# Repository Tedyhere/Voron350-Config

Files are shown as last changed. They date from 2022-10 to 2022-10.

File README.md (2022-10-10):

# Voron350-Config
Config for Voron350 Kit offered by CTRL-Pew

This Kit comes with the PCB Toolboard for the Extruder so be sure to print the Motor Plate for PCB board.
Also print these Parts including the files in the Clockwork folder.
https://github.com/VoronDesign/Voron-Hardware/tree/master/Afterburner_Toolhead_PCB/STLs/Clockwork

For the z Endstop I used the PCB Board Version and drilled 1.5mm holes to match the PCB board for the z endstop in the bottom.

Be sure to check the Parts Cooling and Hotend Fan wire connectors, mine were wire up reverse to what the toolboard required, this is easy to fix, I used a sim card tray tool to push down on the tiny tabs on the connectors and pulled the wires out and swapped them.

You will need to rewire your motors to EXACTLY MATCH the colors on the wiring sheet. I had to extend the B motor on the left side with the Black wire included.  I went ahead and redid both motors to give more length.. I used 4 pin Black connectors included.. Be sure to do 1 wire and connector at a time to ensure you don't cross up wires.  Doing this will make it easier in case a Motor goes bad.

For the Bed you will need to tap the two holes for the Ground and the Thermal fuse.  Follow the directions for the wiring, it seems confusing but..

My heating pad looked like this..

Wires with the wires exiting down.

Left Red wire goes to the Neutral on the Power Supply, the Black is the Thermistor wires, Middle Red I bundled up under the bed and zip tied, Right Red got a Thermal Fuse wired into it and than went to SSR

              R   B   R   R
              |   |   |   |
              |   |   |   |
              |   |   X    \
              |   |         \
              |   |           F
              |   |         /
              |   |       /
              |   |       |
              |   |       |
             PSU Board    SSR

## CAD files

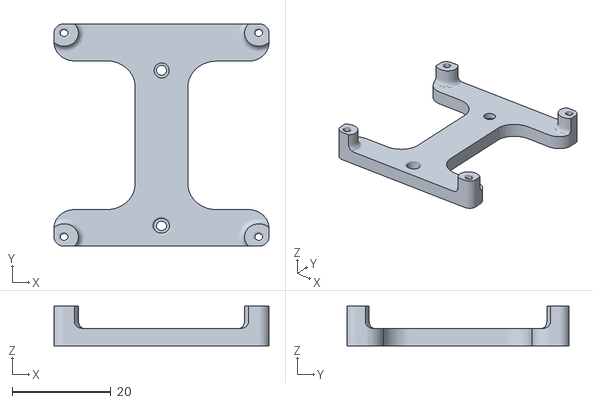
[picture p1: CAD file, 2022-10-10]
OrangePiZeroMount.stl
43.5 x 45.0 x 8.00

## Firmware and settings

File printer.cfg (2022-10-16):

## Voron Design VORON2 250/300/350mm Spider TMC2209 UART config

## *** THINGS TO CHANGE/CHECK: ***
## MCU paths                           [mcu] section
## Thermistor types                    [extruder] and [heater_bed] sections - See https://www.klipper3d.org/Config_Reference.html#common-thermistors for common thermistor types
## Bed sensor_pin                      [heater_bed] section
## Fan pins                            [heater_fan hotend_fan] amd [fan] sections
## Z Endstop Switch location           [safe_z_home] section
## Homing end position                 [gcode_macro G32] section
## Z Endstop Switch  offset for Z0     [stepper_z] section
## Probe points                        [quad_gantry_level] section
## Min & Max gantry corner postions    [quad_gantry_level] section
## PID tune                            [extruder] and [heater_bed] sections
## Fine tune E steps                   [extruder] section

[include mainsail.cfg]
[include client_macros.cfg]
[include stealthburner_led.cfg]

[mcu]
##  Obtain definition by "ls -l /dev/serial/by-id/" 
##--------------------------------------------------------------------
serial: /dev/serial/by-id/usb-Klipper_stm32f446xx_550041000451303439343636-if00

## Uncomment below if you're using the Raspberry uart0 to communicate with Spider
#restart_method: command

[printer]
kinematics: corexy
max_velocity: 400  
max_accel: 11000                 #Max 4000
max_z_velocity: 15          #Max 15 for 12V TMC Drivers, can increase for 24V
max_z_accel: 350
square_corner_velocity: 5.0

#####################################################################
#      X/Y Stepper Settings
#####################################################################

##  Connected to X-MOT (B Motor)
[stepper_x]
step_pin: PE11
dir_pin: PE10
enable_pin: !PE9
rotation_distance: 40
microsteps: 32
full_steps_per_rotation:200  #set to 400 for 0.9 degree stepper
endstop_pin: ^PB14
position_min: 0

##--------------------------------------------------------------------

##  Uncomment below for 250mm build
#position_endstop: 250
#position_max: 250

##  Uncomment for 300mm build
#position_endstop: 300
#position_max: 300

##  Uncomment for 350mm build
position_endstop: 350
position_max: 360

##--------------------------------------------------------------------
homing_speed: 50   #Max 100
homing_retract_dist: 5
homing_positive_dir: true

##  Make sure to update below for your relevant driver (2208 or 2209)
[tmc2209 stepper_x]
uart_pin: PE7
interpolate: False
run_current: 1.0
sense_resistor: 0.110
stealthchop_threshold: 0

##  Connected to Y-MOT (A Motor)
[stepper_y]
step_pin: PD8
dir_pin: PB12
enable_pin: !PD9


rotation_distance: 40
microsteps: 32
full_steps_per_rotation:200  #set to 400 for 0.9 degree stepper
endstop_pin: ^PB13
position_min: 0
##--------------------------------------------------------------------

##  Uncomment for 250mm build
#position_endstop: 250
#position_max: 250

##  Uncomment for 300mm build
#position_endstop: 300
#position_max: 300

##  Uncomment for 350mm build
position_endstop: 350
position_max: 354

##--------------------------------------------------------------------
homing_speed: 50  #Max 100
homing_retract_dist: 5
homing_positive_dir: true

##  Make sure to update below for your relevant driver (2208 or 2209)
[tmc2209 stepper_y]
uart_pin: PE15
interpolate: False
run_current: 1.0
sense_resistor: 0.110
stealthchop_threshold: 0

#####################################################################
#   Z Stepper Settings
#####################################################################

## In Z-MOT Position
## Z0 Stepper - Front Left
[stepper_z]
step_pin: PD14
dir_pin: PD13
enable_pin: !PD15
rotation_distance: 40
gear_ratio: 80:16
microsteps: 32
##  In Z- Position
endstop_pin: ^PA0
##  Z-position of nozzle (in mm) to z-endstop trigger point relative to print surface (Z0)
##  (+) value = endstop above Z0, (-) value = endstop below
##  Increasing position_endstop brings nozzle closer to the bed
##  After you run Z_ENDSTOP_CALIBRATE, position_endstop will be stored at the very end of your config
#position_endstop: 5
##--------------------------------------------------------------------

##  Uncomment below for 250mm build
#position_max: 210

##  Uncomment below for 300mm build
#position_max: 260

##  Uncomment below for 350mm build
position_max: 310

##--------------------------------------------------------------------
position_min: -5
homing_speed: 8
second_homing_speed: 3
homing_retract_dist: 3

##  Make sure to update below for your relevant driver (2208 or 2209)
[tmc2209 stepper_z]
uart_pin: PD10
interpolate: False
run_current: 0.8
sense_resistor: 0.110
stealthchop_threshold: 0

##  In E1-MOT Position
##  Z1 Stepper - Rear Left
[stepper_z1]
step_pin: PE6
dir_pin: !PC13
enable_pin: !PE5
rotation_distance: 40
gear_ratio: 80:16
microsteps: 32

##  Make sure to update below for your relevant driver (2208 or 2209)
[tmc2209 stepper_z1]
uart_pin: PC14
interpolate: False
run_current: 0.8
sense_resistor: 0.110
stealthchop_threshold: 0

##  In E2-MOT Position
##  Z2 Stepper - Rear Right
[stepper_z2]
step_pin: PE2
dir_pin: PE4
enable_pin: !PE3
rotation_distance: 40
gear_ratio: 80:16
microsteps: 32

##  Make sure to update below for your relevant driver (2208 or 2209)
[tmc2209 stepper_z2]
uart_pin: PC15
interpolate: False
run_current: 0.8
sense_resistor: 0.110
stealthchop_threshold: 0

##  In E3-MOT Position
##  Z3 Stepper - Front Right
[stepper_z3]
step_pin: PD12
dir_pin: !PC4
enable_pin: !PE8
rotation_distance: 40
gear_ratio: 80:16
microsteps: 32

##  Make sure to update below for your relevant driver (2208 or 2209)
[tmc2209 stepper_z3]
uart_pin: PA15
interpolate: False
run_current: 0.8
sense_resistor: 0.110
stealthchop_threshold: 0

#####################################################################
#   Extruder
#####################################################################

##  In E0-MOT Position
[extruder]
step_pin: PD5
dir_pin: PD6
enable_pin: !PD4

##  Update value below when you perform extruder calibration
##  If you ask for 100mm of filament, but in reality it is 98mm:
##  rotation_distance = <previous_rotation_distance> * <actual_extrude_distance> / 100
##  22.6789511 is a good starting point for Bondtech 5mm gears
##  34.37086 for Bondtech 8mm gears (Galileo)
rotation_distance: 22.6789511   #Bondtech 5mm Drive Gears
##  Update Gear Ratio depending on your Extruder Type
##  Use 50:17 for Afterburner/Clockwork (BMG Gear Ratio)
##  Use 80:20 for M4, M3.1
##  Use 7.5:1 for Galileo
gear_ratio: 50:17               #BMG Gear Ratio
microsteps: 32
full_steps_per_rotation: 200    #200 for 1.8 degree, 400 for 0.9 degree
nozzle_diameter: 0.400
filament_diameter: 1.75
##      In E0 OUT Position
heater_pin: PB15
## Check what thermistor type you have. See https://www.klipper3d.org/Config_Reference.html#common-thermistors for common thermistor types.
## Use "Generic 3950" for NTC 100k 3950 thermistors
sensor_type: Generic 3950
sensor_pin: PC0
min_temp: 10
max_temp: 320
max_power: 1.0
min_extrude_temp: 170
#control = pid
#pid_kp = 26.213
#pid_ki = 1.304
#pid_kd = 131.721
##  Try to keep pressure_advance below 1.0
#pressure_advance: 0.05
##  Default is 0.040, leave stock
#pressure_advance_smooth_time: 0.040

##  In E0-MOT Position
##  Make sure to update below for your relevant driver (2208 or 2209)
[tmc2209 extruder]
uart_pin: PD7
interpolate: false
run_current: 0.5
sense_resistor: 0.110
stealthchop_threshold: 0

#####################################################################
#   Bed Heater
#####################################################################
##  SSR Pin - In BED OUT position
[heater_bed]
heater_pin: PB4
## Check what thermistor type you have. See https://www.klipper3d.org/Config_Reference.html#common-thermistors for common thermistor types.
## Use "Generic 3950" for Keenovo heaters
sensor_type: Generic 3950

##--------------------------------------------------------------------
##  Select the option that matches your board
#sensor_pin: PC3 # Spider 1.0 & 1.1
sensor_pin: PB0 # Spider 2.2
##--------------------------------------------------------------------

##  Adjust Max Power so your heater doesn't warp your bed
max_power: 0.8
min_temp: 0
max_temp: 120
#control: pid
#pid_kp: 58.437
#pid_ki: 2.347
#pid_kd: 363.769

#####################################################################
#   Probe
#####################################################################

##  This probe is not used for Z height, only Quad Gantry Leveling
##  In Z+ position
[probe]
##  If your probe is NO instead of NC, change pin to ^!PA3
pin: ^!PA3
x_offset: 0
y_offset: 25.0
z_offset: 0
speed: 10.0
samples: 5
samples_result: median
sample_retract_dist: 3.0
samples_tolerance: 0.010
samples_tolerance_retries: 3

#####################################################################
#   Fan Control
#####################################################################
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

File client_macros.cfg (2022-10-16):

[gcode_macro LOAD_FILAMENT]
gcode:
   M83                            ; set extruder to relative
   G1 E30 F300                    ; load
   G1 E15 F150                    ; prime nozzle with filament
   M82                            ; set extruder to absolute
    
[gcode_macro UNLOAD_FILAMENT]
gcode:
   M83                            ; set extruder to relative
   G1 E10 F300                    ; extrude a little to soften tip
   G1 E-40 F1800                  ; retract some, but not too much or it will jam
   M82                            ; set extruder to absolute

#####################################################################
#   Macros
#####################################################################
[gcode_macro PRIMING]
gcode:
    M106 S255                      ;partcooling fan max             .1
    CLEAN                          ;call clean macro                .2
    G1  X180 Y0 F30000              ;move to purge position    X/Y  .3
    G1  Z0.3 F5000                  ;move to purge position    Z    .4
    G91                            ;incremental positioning         .5
    G1  E14 F500                   ;prime hotend                    .6
    G1  Z10 E25 F250               ;purge and move up               .7
    G1  Z10 F5000                  ;move up by 10                   .8
    G1  X-30 Z-20.1 F5000          ;move to wiping start      X/Z   .9
    G1  X-20                       ;wipe end                    X   .10
    G1  Z10  F5000                 ;move up                         .11
    M82                            ;extruder absolute               .12
    G92 E0.0                       ;extruder reset                  .13               
    G90                            ;absolute positioning            .14
    M107                           ;partcooling fan off             .15

[gcode_macro CLEAN]
gcode:
    M204 S6000                     ;set acceleration to 6000        .16
    G1 X180 Y30 F30000             ;move to position          X/Y   .17
    G1 Z0.8 F5000                  ;move to position          Z     .18
    G1 Y0 F30000                   ;kik the prime tower off         .19
[gcode_macro PARK]
gcode:
    G1 X10 Y5
    G1 Z10
    G1 Z0 F1000


[gcode_macro G32]
gcode:
    SAVE_GCODE_STATE NAME=STATE_G32
    G90
    G28
    QUAD_GANTRY_LEVEL
    G28
    ##  Uncomment for for your size printer:
    #--------------------------------------------------------------------
    ##  Uncomment for 250mm build
    #G0 X125 Y125 Z30 F3600
    
    ##  Uncomment for 300 build
    #G0 X150 Y150 Z30 F3600
    
    ##  Uncomment for 350mm build
    G0 X175 Y175 Z30 F3600
    #--------------------------------------------------------------------
    RESTORE_GCODE_STATE NAME=STATE_G32

#   Use PRINT_START for the slicer starting script - please customise for your slicer of choice
[gcode_macro PRINT_START]
gcode:


      g90
      #Get Printer built volume dimensions
      {% set X_MAX = printer.toolhead.axis_maximum.x|default(100)|float %}
      {% set Y_MAX = printer.toolhead.axis_maximum.y|default(100)|float %}
      {% set Z_MAX = printer.toolhead.axis_maximum.z|default(100)|float %}

      #Get Nozzle diameter and filament width for conditioning
      {% set NOZZLE = printer.extruder.nozzle_diameter|default(0.4)|float %}
      {% set FILADIA = printer.extruder.filament_diameter|default(1.75)|float %}

      #Set Start coordinates of priming lines
      {% set X_START = 5.0|default(10.0)|float %}
      {% set Y_START = 1.0|default(20.0)|float %}

      #Calculate Primer line extrusion volume and filament length
      {% set PRIMER_WIDTH = 0.75 * NOZZLE %}                    
      {% set PRIMER_HEIGHT = 0.70 * NOZZLE %}           
      {% set PRIMER_SECT = PRIMER_WIDTH * PRIMER_HEIGHT %}    
      {% set PRIMER_VOL = PRIMER_SECT * (X_MAX - 3 * X_START) %}    
      {% set FILA_SECT = 3.1415 * ( FILADIA / 2.0)**2 %}          
      {% set FILA_LENGTH = 1.55 * PRIMER_VOL / FILA_SECT %}      

      #Get Bed and Extruder temperature from Slicer GCode
      {% set BED_TEMP = params.BED_TEMP|default(60)|float %}
      {% set EXTRUDER_TEMP = params.EXTRUDER_TEMP|default(190)|float %}
      {% set CHAMBER_TEMP = params.CHAMBER_TEMP|default(0)|float %}
                                      
      #Home
    STATUS_HOMING
    G28 ; home all axes
    # QGL if not already QGLd (only if QGL section exists in config)
		{% if printer.configfile.settings.quad_gantry_level %}
			{% if printer.quad_gantry_level.applied == False %}
				QUAD_GANTRY_LEVEL
				G28 Z
			{% endif %}
		{% endif %}	
    G90                            ; absolute positioning
    G1 Z20 F3000                   ; move nozzle away from bed 

      #Heat bed
      STATUS_HEATING
      M117 Heating Bed
      M190 S{BED_TEMP}  
      STATUS_MESHING
      M117 Probing Bed
      G0 X50 Y25
      BED_MESH_CALIBRATE 
      STATUS_HOMING

      G28

        

      #Precondition extruder
      M117 Heating Extruder
      STATUS_HEATING
      PARK
      M109 S{EXTRUDER_TEMP} T0
      M117 Priming
      G1 Z10
      PRIMING
      STATUS_BUSY
      M117 Printing

#   Use PRINT_END for the slicer ending script - please customise for your slicer of choice
[gcode_macro PRINT_END]
#   Use PRINT_END for the slicer ending script - please customize for your slicer of choice
gcode:
    M400                           ; wait for buffer to clear
    G92 E0                         ; zero the extruder
    G1 E-4.0 F3600                 ; retract filament
    G91                            ; relative positioning

    #   Get Boundaries
    {% set max_x = printer.configfile.config["stepper_x"]["position_max"]|float %}
    {% set max_y = printer.configfile.config["stepper_y"]["position_max"]|float %}
    {% set max_z = printer.configfile.config["stepper_z"]["position_max"]|float %}

    #   Check end position to determine safe direction to move
    {% if printer.toolhead.position.x < (max_x - 20) %}
        {% set x_safe = 20.0 %}
    {% else %}
        {% set x_safe = -20.0 %}
    {% endif %}

    {% if printer.toolhead.position.y < (max_y - 20) %}
        {% set y_safe = 20.0 %}
    {% else %}
        {% set y_safe = -20.0 %}
    {% endif %}

    {% if printer.toolhead.position.z < (max_z - 2) %}
        {% set z_safe = 2.0 %}
    {% else %}
        {% set z_safe = max_z - printer.toolhead.position.z %}
    {% endif %}

    G0 Z{z_safe} F3600             ; move nozzle up
    G0 X{x_safe} Y{y_safe} F20000  ; move nozzle to remove stringing
    TURN_OFF_HEATERS
    M107                           ; turn off fan
    G90                            ; absolute positioning
    G0 X60 Y{max_y} F3600  ; park nozzle at rear
    M117 Print Finished


# Home, get position, throw around toolhead, home again.
# If MCU stepper positions (first line in GET_POSITION) are greater than a full step different (your number of microsteps), then skipping occured.
# We only measure to a full step to accomodate for endstop variance.
# Example: TEST_SPEED SPEED=300 ACCEL=5000 ITERATIONS=10
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

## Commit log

2022-10-10 Added voron350.cfg and client_macros.cfg
    [Voron350.cfg, client_macros.cfg]
2022-10-10 Update client_macros.cfg
    ADDED a Priming MACRO.. It will print a small blob and than kick it off the plate. a Purge bucket is recommended.
    I used this one
    https://www.printables.com/model/291878-purge-tray-with-v24-purge-macro
    [client_macros.cfg]
2022-10-10 Orange Pi Zero Mount
    Added OrangePi Zero Mount
    [OrangePiZeroMount.stl]
2022-10-13 Add files via upload
    Updated Macros and Added a Test_Speed Macro to determine max speed and accel.
    [client_macros.cfg]
2022-10-15 cline_macros.cfg
    Updated to replace an errant G Code with the proper M Code
    [client_macros.cfg]
2022-10-16 Replaced client_macros.cfg
    [client_macros.cfg]
2022-10-16 My current printer.cfg file
    [printer.cfg]
